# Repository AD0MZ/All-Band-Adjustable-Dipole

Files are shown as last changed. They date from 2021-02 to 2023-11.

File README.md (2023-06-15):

# All-Band-Adjustable-Dipole
### Motorized 10-80 Meter Adjustable Dipole 

-  A Self-Contained – Motorized Dipole Antenna System
-  Uses a Web-Based APP to set Element Lengths.  
-  Robust support for CAT and other Automation
-  Open Source – Using Open Source Tools

# Finished Product and APP!
- Antenna Winch on Tripod Mount.
  - Can Hang From a Rope or Use the Pole Mount Accesory.
- Node-Red Dashboard APP.  On Pixel 3 (Medium sized phone).

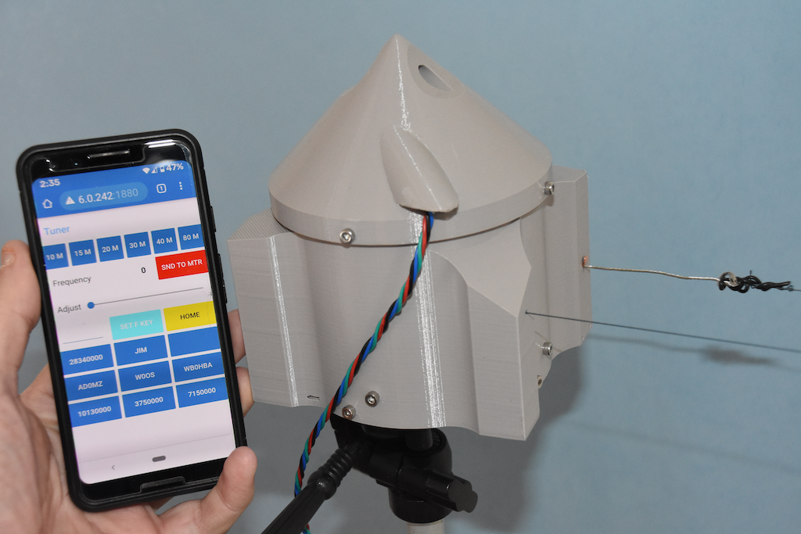
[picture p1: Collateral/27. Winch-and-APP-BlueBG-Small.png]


##### Inspiration
  - Interested in Antenna Physics since High School.
    - Particularly the concepts of Gain and Directivity when considering conservation of energy.
  - Recently interested in how Resonance and SWR affect Efficient Radiation.
  - Was surprised at how much better a friend’s antenna performed after a slight pruning.
    - We both noted how much better his dipole worked compared to his G5RV or his HexBeam Spiderweb.
  - Began thinking of an “automatic” self-pruning-dipole.
  - Hangar Door Openers!  
    - Realized that a creatively constructed “Capstan” combined with a clothesline-like element geometry would simplify the mechanics.
    - Airplane hangar door openers use a wire and drum geometry, and are the mechanical inspiration for the prototypes.
  - Needed a good Winter Project during “Covid - Stay at home”.

##### Learning from Those That Have Gone Before.
  - Article by AE4YW – Radiation is more important than SWR.
  - The RTV 80 by W4QJP and KC4TAQ  is a proven example of a complete adjustable system (But manually operated with adjustable ropes).
  - VA2ERY used a literal incarnation of a clothesline to move the feed-point of a folded dipole.
    - (Simple, but requires a balanced feed-line and a tuner.)
  - Collins Aerospace dual-drum winch for wire dipoles (Model 637-T1).
  - SteppIr.  Very successful stepper motor controlled Yagi’s, etc.
    - An automated – multi-element “Tape Measure” system if you look inside.

#### Status:  Two protoypes constructed and tested.  
  - Ready for constructive input and suggestions for improvement.  (More weatherproof?  Better / Simpler Stepper Control?  Etc?)

**Disclaimer:  I am a beginner with the tools I chose for this project, so it's as much a learning process as a production process.
  - I spent a lot of time quantifying and tuning my printer to make accurate parts.  The SCAD and STL files in this repository reflect
    pretty tight tolerances.  (The parts from my Prusa Mk3S had a nice friction fit and assembled without modification.)
    - (Parts printed on my friends Ender Pro were too big and required sanding and filing.)
    - If you use the STL's, print the first three layers of a few of the parts to see if things fit.

#### Tools Used:
  - OpenSCAD.  Wanted to learn it.  Experienced TurboCad Deluxe user, but it lacks proper 3D tools.
    - Tried FreeCad, but found it cumbersome.  (Tried others, but like the program-like build process.  Minutes to first useful object.
  - TurboCad.  Useful for initial 2D design to get precise measurements.
  - Wifi-Stepper Controller:  As a beginner with stepper control, Advanced feactures like acceleration and crash detection were beyond me.
    - The Wifi Stepper removes the complexity of comprehensive control and also provides simple interaces.  HTML, Bash, and Mqtt.

# Initial Concept:

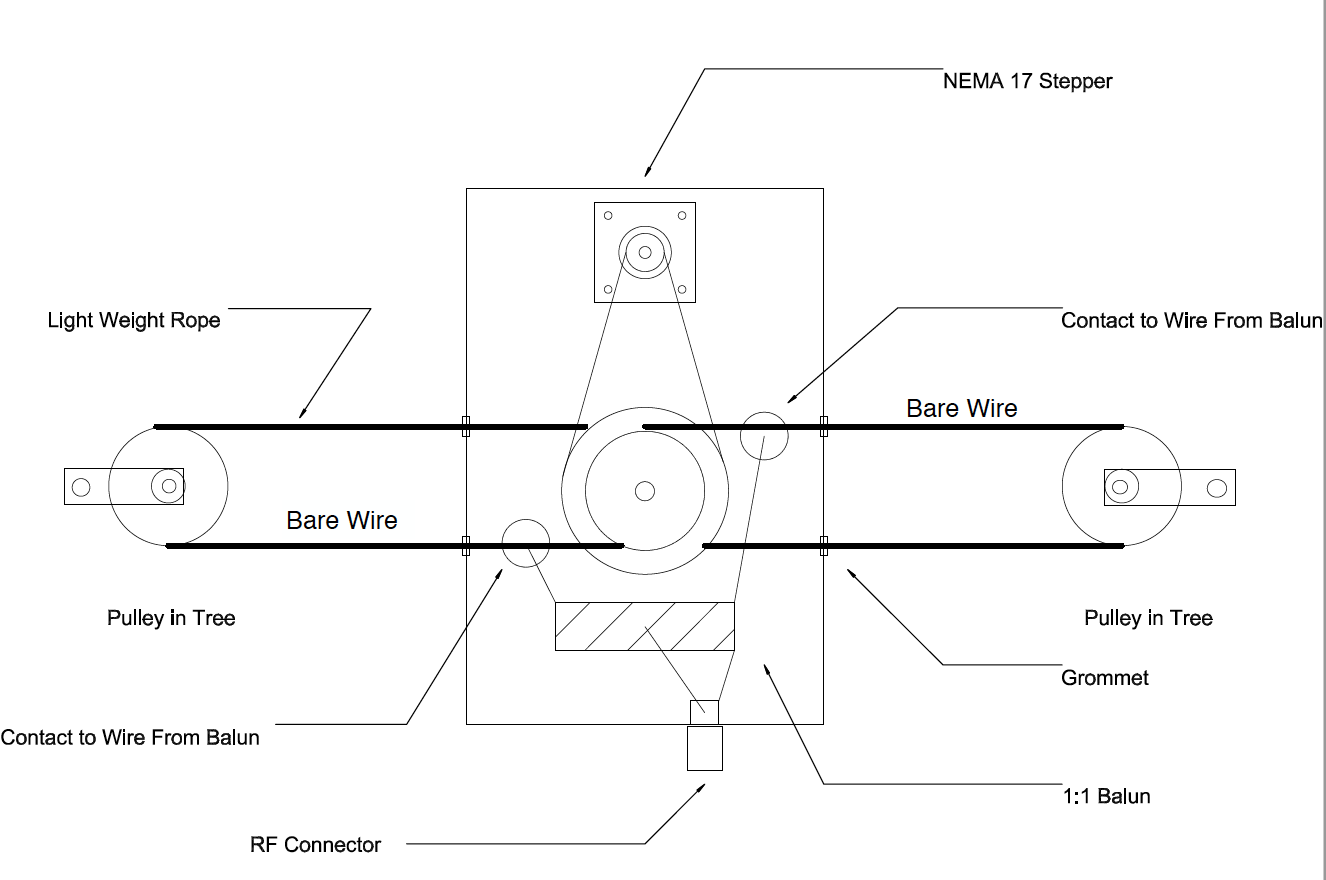
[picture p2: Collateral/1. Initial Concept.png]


# Animation of Kinematics
### Note that the wire (end at red dot) is wound out as a thin rope (Braided 60lb Fishing Line) is wound in (and in reverse).

All Band Adjustable Dipole

# Animation of a Sample Application.  (Node-Red Dashboard)

- The Flow lets the user select a band, then fine adjust it.  
  - A simple function calculates steps via simple math, and sends an absolute position to the motor. 
  
All Band Adjustable Dipole

# Bom:
  - (1) 8x22x7 MM sealed skateboard bearing
  - Assorted M3 screws and 16 thin square M3 nuts.
    - (14) M3-10 Button Head Screws (or cap-screws).
    - (4) M3-35 Button Head Screws (or cap-screws).
    - (16) M3 562 (S2) Thin - Flat Square nuts.
    - (2) M3 hex nuts.
  - (2) Generic (Makita CB-303 in my case) power tool brushes.
  - ~ 130 feet of 18 gauge tinned (less oxidation) wire.
  - ~ 260 feet of Nylon or Dacron 60lb test fishing line.
  - (4) pulleys (you can print them too), and some lightweight rope.
  - (2) 4mm x 1mm x 31mm copper strips.  (Wire guide slide surfaces.)
  - Glue compatible with plastic type.  (Top fasten top spool to middle spool.  Alignment pegs are on parts.)
    - Could add bosses and holes for screws on this part - was nervous about clearance for first unit. 
    - Bosses and holes on the improvement list.  (The part broke before the glue let go in my testing.)
  
  - Time to print:  ~40 hours.

  # Cutaway view of Internal Capstan Parts.
  
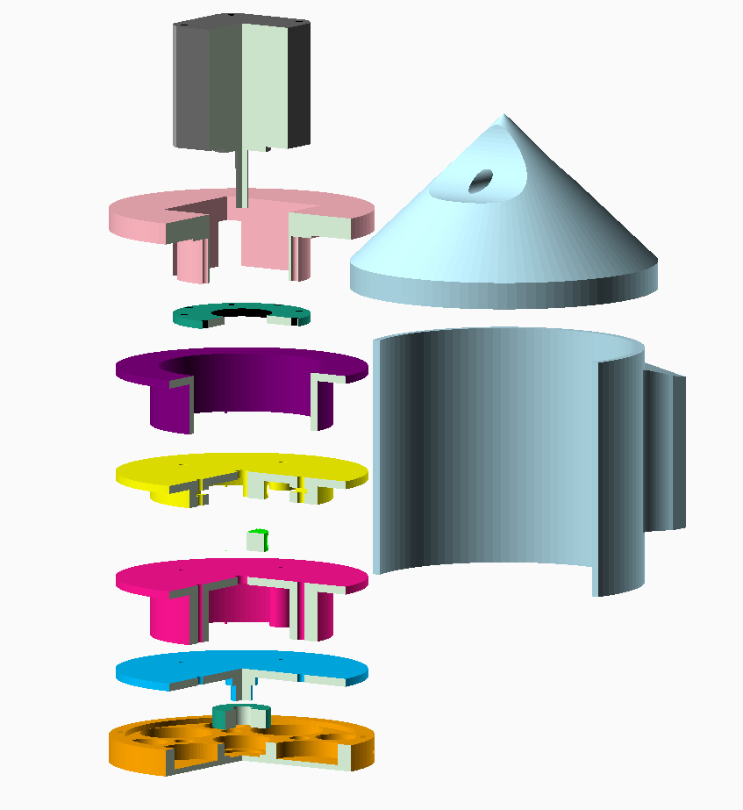
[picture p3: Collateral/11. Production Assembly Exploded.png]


# First Printed Parts
### Note:  First 3DP project! Trying different things.

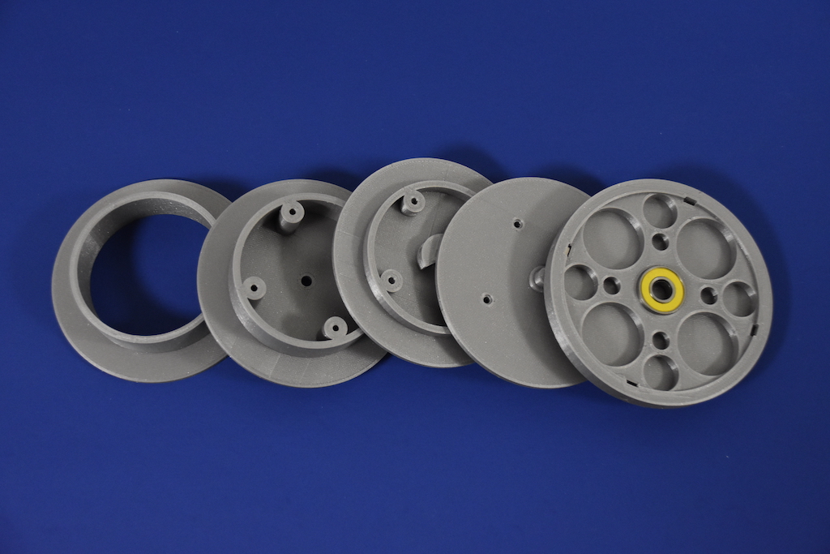
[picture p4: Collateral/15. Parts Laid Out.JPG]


# Brush Cartridge
- External for easy replacement.
  - Wires from balun or coax connect to cartridge only.  (Hole in bottom)
  - Optional base can house a balun or other gear, wire feeds through bottom of both parts to prevent water ingress.

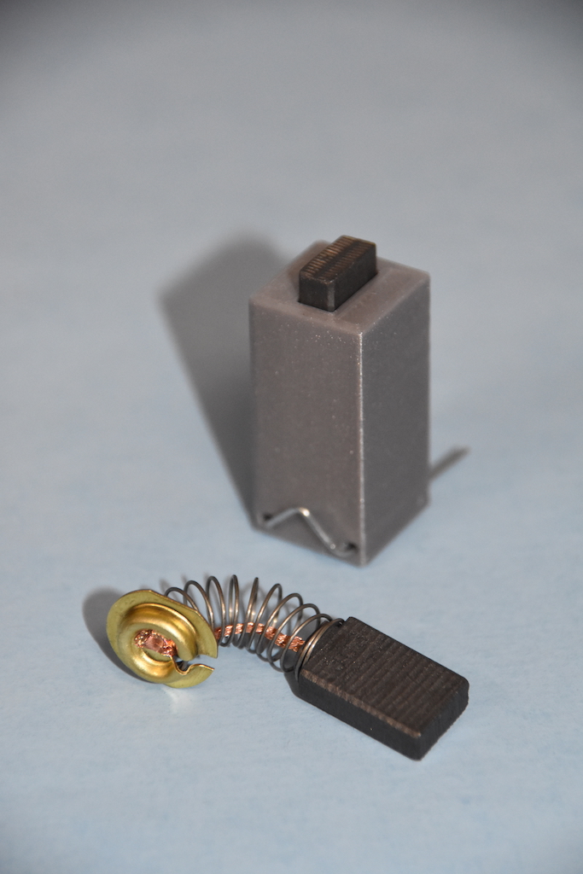
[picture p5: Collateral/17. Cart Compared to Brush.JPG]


# Brush Cartridges in place (almost) with Pole Mount and Balun Housing in place.  
- Housing pushed in to show brush carts better!

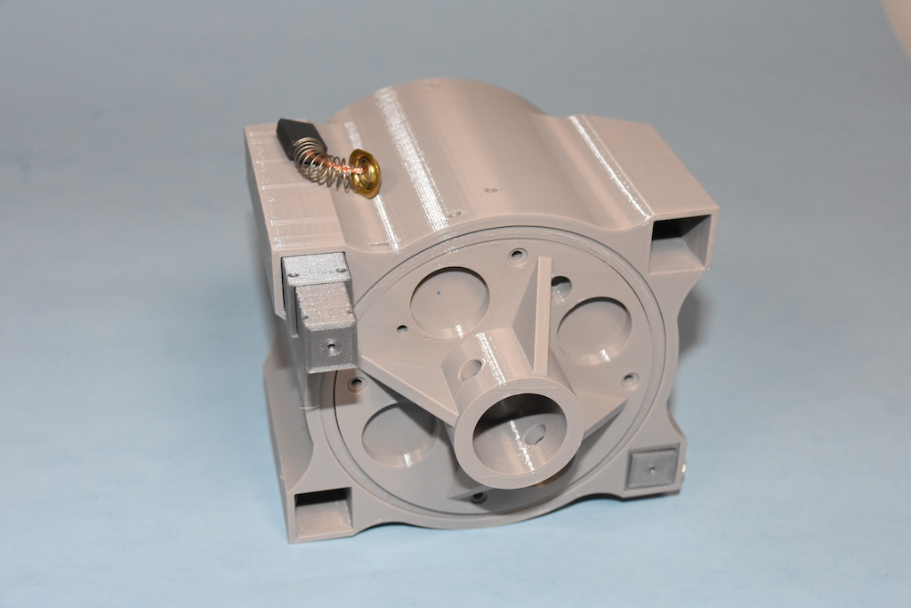
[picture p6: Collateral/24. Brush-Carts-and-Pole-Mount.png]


# VNA (un-calibrated :-)  ) scanning 13Mhz to 15Mhz when antenna is tuned to 14.220 Mhz

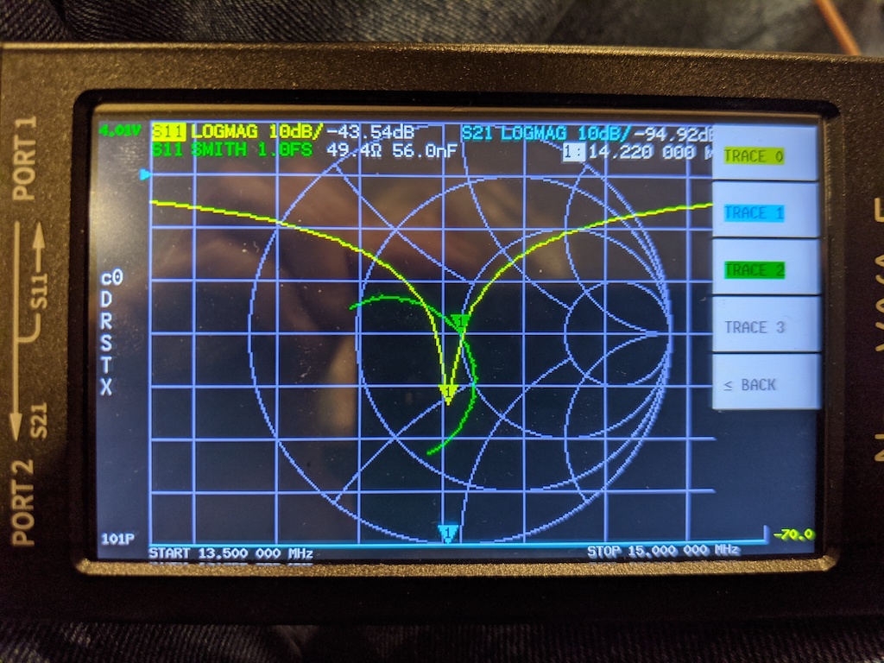
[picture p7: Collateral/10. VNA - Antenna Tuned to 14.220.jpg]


# Similar Antennas / Prior Work
- Collins 637t-1.
- Center Adjustable Folded Clothesline Dipole.
- RTV 80 Inverted V.

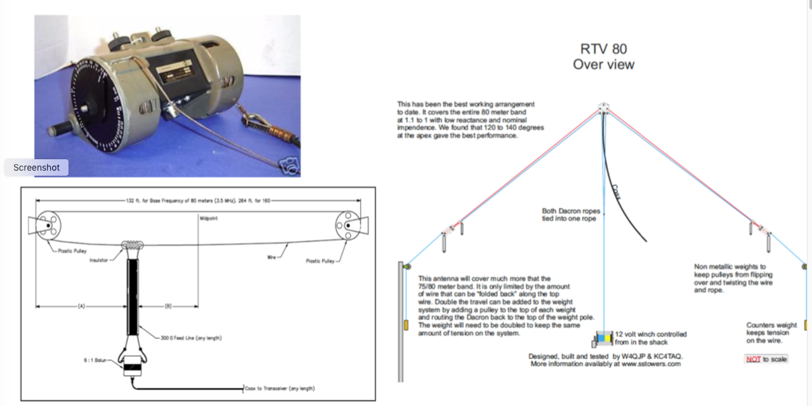
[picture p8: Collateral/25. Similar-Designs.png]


# Winch / Controller Closeup.

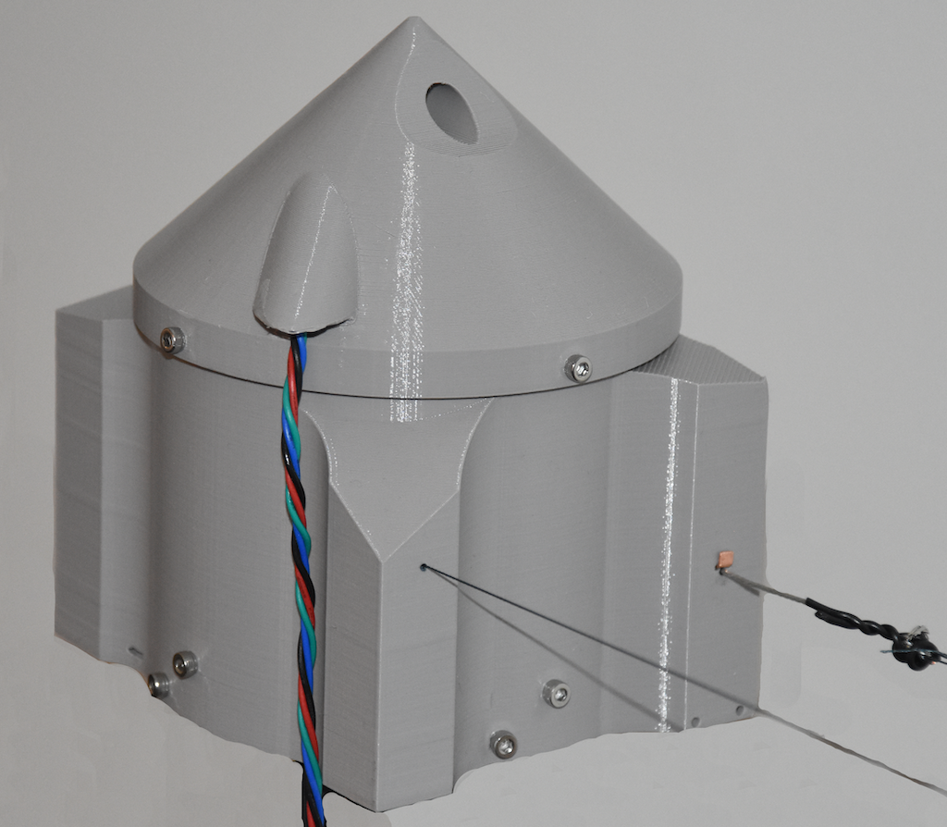
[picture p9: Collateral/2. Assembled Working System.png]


# Arrangement of commutators (brushes) with elements (wires).
- A few people have asked me why the brushes are on the "outside" of the capstan mechanism.
- One friend asked about the use of bare wire rather than insulated.
    - It turns out that the location of the brushes and the issues of insulated (or un-insulated) wire are related.

Early on, I had envisioned internal brushes on a commutating ring like an automotive alternator, 
with the use of insulated wire elements.
- I soon realized that the coiled-up element wires would make an excellent inductor at the frequencies we operate at.
- I was uncertain of how the brushes would wear, and how certain meterials might conduct at RF. 
    - I wanted to have an easy way to change them and experiment.
- Using un-insulated wire and external brushes solved every fatal problem and only introduced a couple of minor ones.
    _ (1.  Corrosion    2.  Loss of signal to things that touch the wire like leaves? )
    
Here are two diagrams I used to demonstrate the issues to a very smart friend.

Final design:
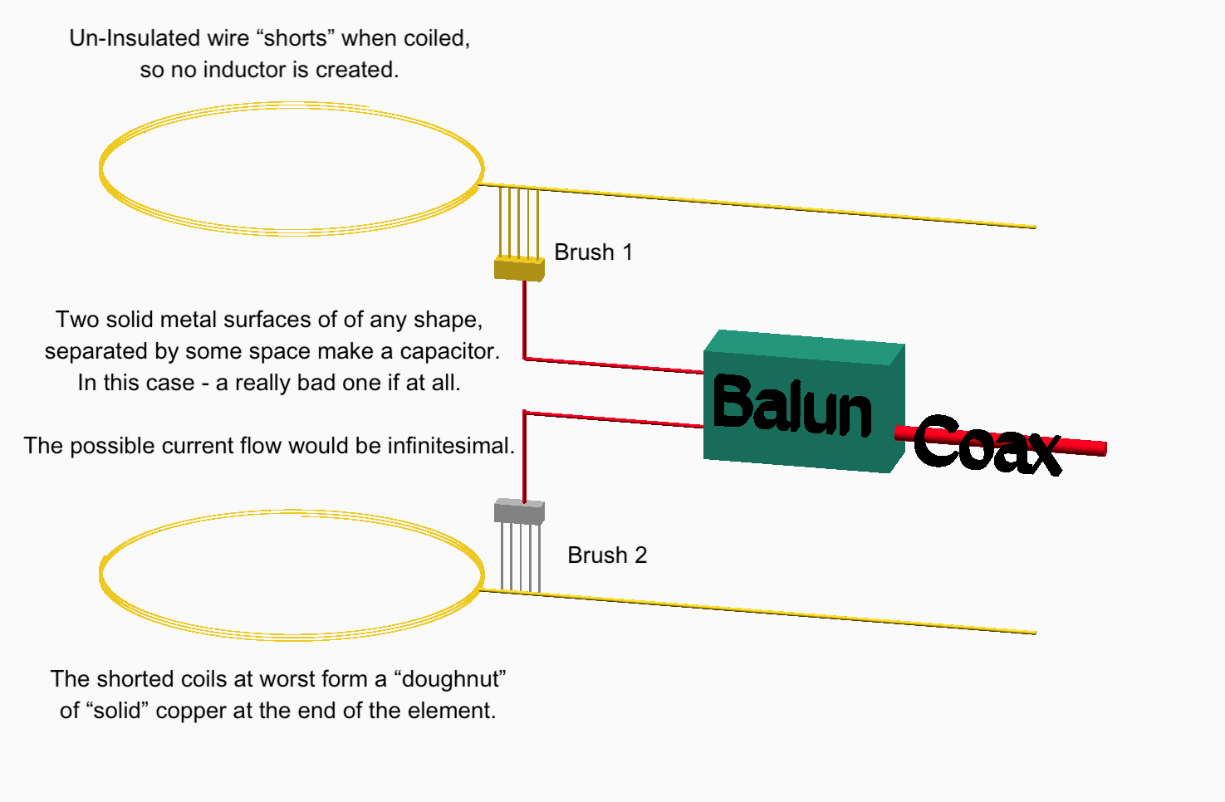
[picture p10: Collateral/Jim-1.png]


Contemplated design:
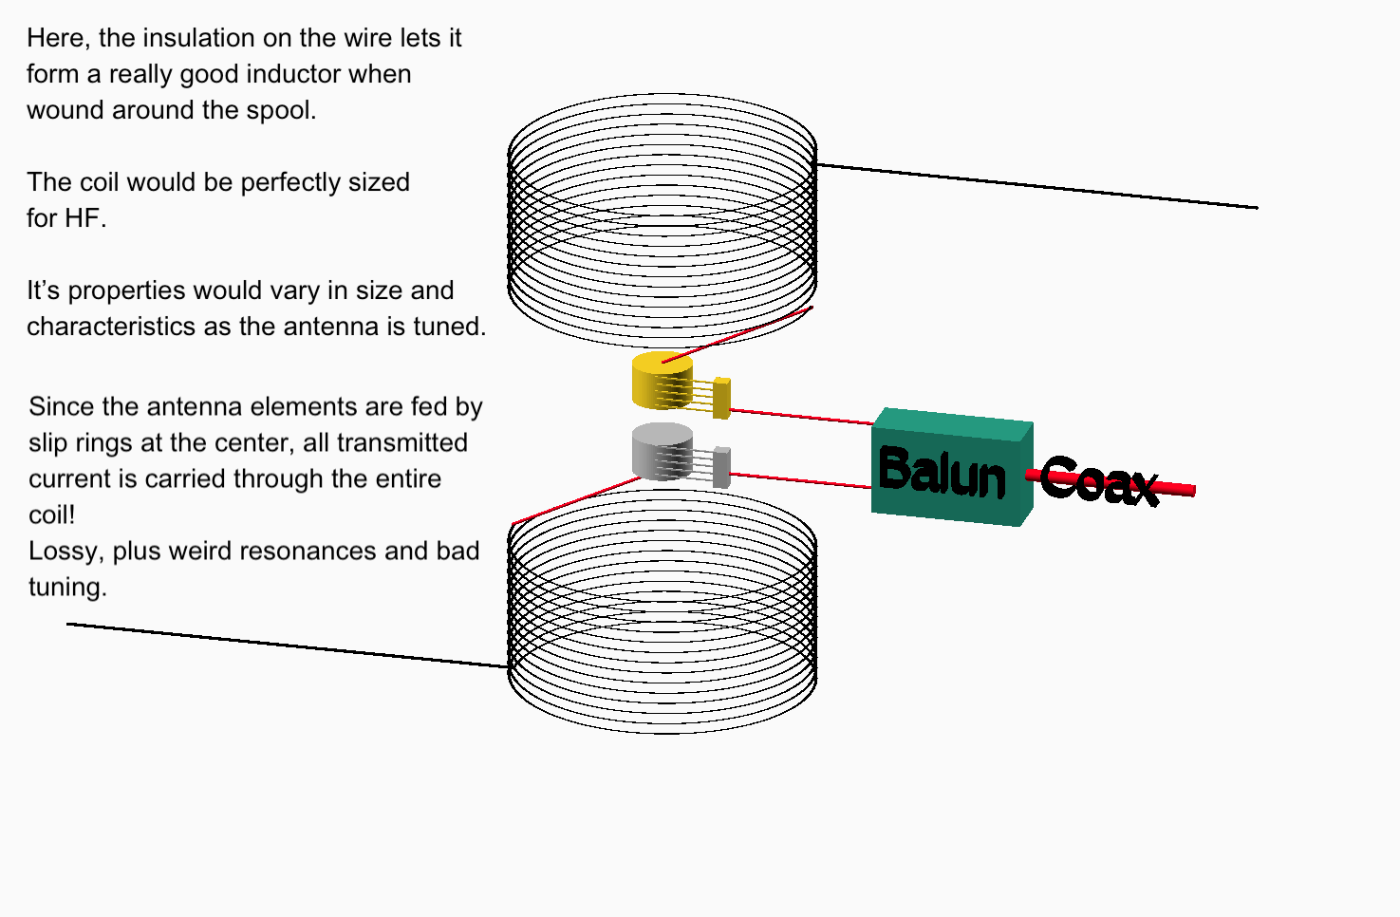
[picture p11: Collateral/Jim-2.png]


# It would be fun to model the "insulated wire - central commutator" design to see if it would be tunable across all bands with wierd  but shorter element lengths.
- Software could then pick the memorized lengths for each band with micro-tuning control still available.
- The coiled wire on spools could act as loading coils, with more coil at shorter element lengths.

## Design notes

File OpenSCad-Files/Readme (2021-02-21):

# The various plastic parts.

## This is my first OpenSCAD project, so I learned as I went.

### Planned work.

1.  Improve and spell check to comments, adding better documentation of pourpose and better explaination of spaghetti code.
2.  Start cleaning up variouis modules to better paraterize them, including more constants with variables in constructs.
    - First functional improvment - add some holes in the flanges of the spools to make ataching the wires and ropes without disassembly is possible and easy.

#### The topmost capstan parts were the first to be modeled, working towards the bearing plate, and the back up to the motor mount.
     - I hope to redo them all to be more "paramterized" and more modular.  (Lots of spaghetti code on some...)  
     - Will go though them as time permits and improve the comments as well.
  
- My workflow...  (Some not implemented yet  :-)   )
  - Draw the proposed system in 2D using TurboCad to get good measurements and to help visualize.
    - Tried FreeCad, TinkerCad, and others - the learining curve was too steep after 20 years of TurboCad.
      -  After two days with FreeCad and giving up,  Had a set of capstan spools completed with OpenSCAD in a few hours!
  - Design the solid parts and combine into a module.
  - Design the shapes that will be subtracted for holes and such and place into a module or two.
  - Combine the two into another module with "difference ()"
  - Call out the main module so it shows.
  - Try to use unique names (not competed) so that "include" can be used to assemble parts into views easier.

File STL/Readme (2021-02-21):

The main case file gives a manifold error in OpenSCAD, util a very minor hole is eliminated.  (Screw_holes).
Other tools proclaim it OK, and it prints fine.  On the list to debug further, but since I dropped the entire tuner onto concrete from high up and cracked it - I wanted to reprint instead of debug.

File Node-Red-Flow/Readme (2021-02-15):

The Main Flow for the Tuner, and a test set of utilities to set controller parameters.

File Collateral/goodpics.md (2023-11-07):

<table>
<tr>
<th>1970's Sansui 55 Watt Audiopile Amp  </td>
<th>Print of Famous Guardian Angel Painting</td>
<th>15 Speed Bike</br>Was called a "Girls Bike" back in the days.</td>
</tr>

<tr>
<td valign="top">
<a href="./GoodPics/Amp.jpg">
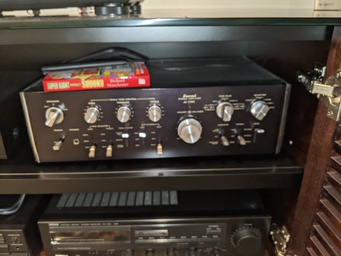
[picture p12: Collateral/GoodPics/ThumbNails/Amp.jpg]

</a>
</td>

<td valign="top">
<a href="./GoodPics/Angel-Guide.jpg">
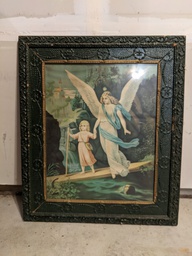
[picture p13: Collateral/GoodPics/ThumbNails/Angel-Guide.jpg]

</a>
</td>

<td valign="top">
<a href="./GoodPics/BIke.jpg">
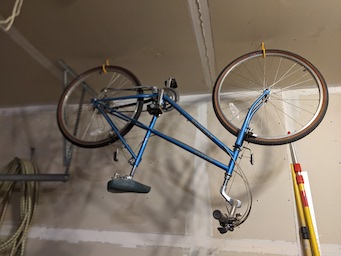
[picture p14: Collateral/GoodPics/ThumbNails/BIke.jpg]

</a>
</td>
</table>

<table>
<tr>
<th>Full-Featured Bernina Sewing Machine (Value Model) </td>
<th>Classic 8mm Bolex Movie Camera</td>
<th>Same Bolex showing four lenses</td>
</tr>

<tr>
<td valign="top">
<a href="./GoodPics/Bernina.jpg">
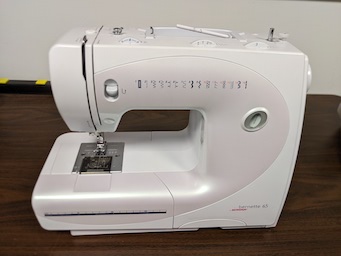
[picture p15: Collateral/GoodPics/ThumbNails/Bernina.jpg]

</a>
</td>

<td valign="top">
<a href="./GoodPics/Bolex-1.jpg">
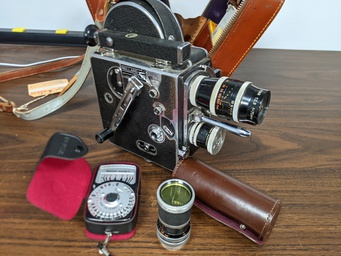
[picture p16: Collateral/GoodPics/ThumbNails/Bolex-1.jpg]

</a>
</td>

<td valign="top">
<a href="./GoodPics/Bolex-2.jpg">
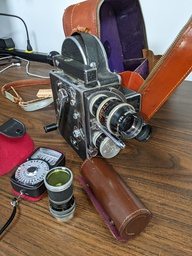
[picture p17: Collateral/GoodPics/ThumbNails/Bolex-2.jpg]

</a>
</td>

</table>

<table>
<tr>
<th>Original Box for Bolex</td>
<th>Yamaha Cassette Player (Part of Component Set)</td>
<th>Antique Corn Planter (Really old)</td>
</tr>
  
<tr>
<td valign="top">
<a href="./GoodPics/Bolex-3.jpg">
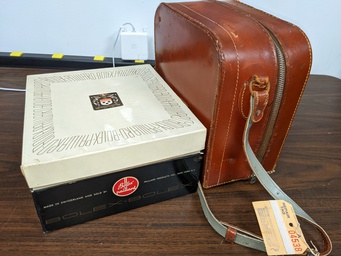
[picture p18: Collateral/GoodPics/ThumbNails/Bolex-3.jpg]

</a>
</td>

<td valign="top">
<a href="./GoodPics/Cassette.jpg">
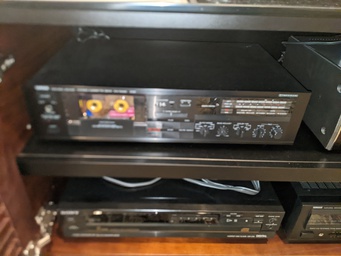
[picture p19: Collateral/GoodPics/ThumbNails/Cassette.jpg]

</a>
</td>

<td valign="top">
<a href="./GoodPics/Corn-Planter.jpg">
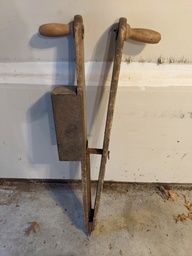
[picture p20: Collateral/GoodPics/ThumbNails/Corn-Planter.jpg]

</a>
</td>
</tr>

</table>

<table>
<tr>
<th>Portrait of Euphamia Strandjord (I Think)</td>
</tr>
  <tr>
<td valign="top">
<a href="./GoodPics/Euphamia.jpg">
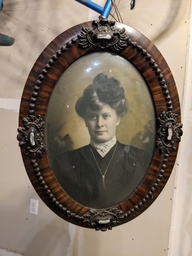
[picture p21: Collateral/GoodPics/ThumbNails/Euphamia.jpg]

</a>
</td>
</tr>
</table>

<table>

<tr>
<th>Mac Pro - Core Duo</br> New battery</br>Clean HD + MSOFFICE</br>Good for email and web)</td>
<th>Yamaha Receiver (part of set)</td>
<th>Shop Vac</td>
</tr>

<tr>
<td valign="top">
<a href="./GoodPics/Mac-Pro.jpg">
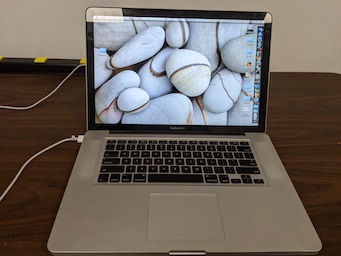
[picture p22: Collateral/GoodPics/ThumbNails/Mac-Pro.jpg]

</a>
</td>

<td valign="top">
<a href="./GoodPics/Receiver.jpg">
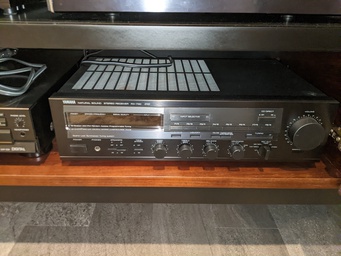
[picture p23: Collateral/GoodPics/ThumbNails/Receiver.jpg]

</a>
</td>

<td valign="top">
<a href="./GoodPics/Shop-Vac.jpg">
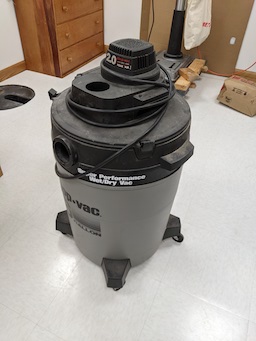
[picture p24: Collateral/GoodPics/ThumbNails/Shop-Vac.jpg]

</a>
</td>

</table>

<table>
<tr>

<th>Singer Featherweight (Restored)</td>
  <th>Sony 5 disk CD Player</th>
</tr>

<tr>

<td valign="top">
<a href="./GoodPics/Singer.jpg">
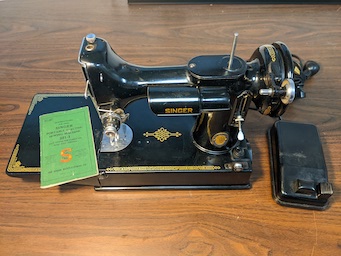
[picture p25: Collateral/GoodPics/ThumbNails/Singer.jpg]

</a>
</td>

<td valign="top">
<a href="./GoodPics/Sony-CD.jpg">
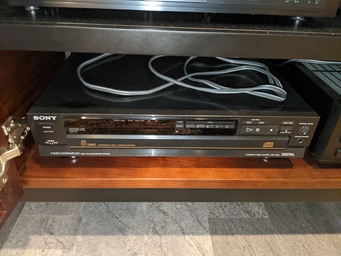
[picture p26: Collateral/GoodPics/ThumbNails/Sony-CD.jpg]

</a>
</td>
</tr>

</table>

<table>
<tr>
<th>Speakers - Klipsh Forte  </br>Mellow -- Classical Music, on left)</br></br> Keeping the Classic Pioneer HPM 100's </br>Google Them!</br>(Crisp -- Rock, etc. on  right)</td>
<th>Lenovo T510 Busines Class Laptop</br> (As new - Clean)</td>
<th>Table Saw (Recently refurbished)</td>
</table>tr>
<tr>
<td valign="top">
<a href="./GoodPics/Speakers.jpg">
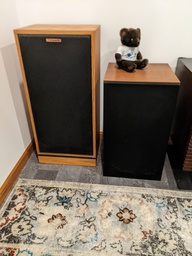
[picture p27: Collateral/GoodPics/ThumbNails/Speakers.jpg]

</a>
</td>

<td valign="top">
<a href="./GoodPics/T510.jpg">
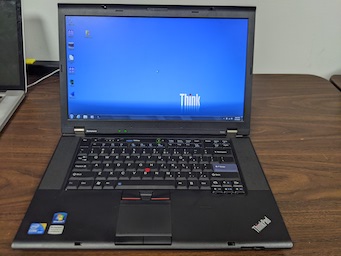
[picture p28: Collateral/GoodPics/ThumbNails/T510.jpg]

</a>
</td>

<td valign="top">
<a href="./GoodPics/Table-Saw.jpg">
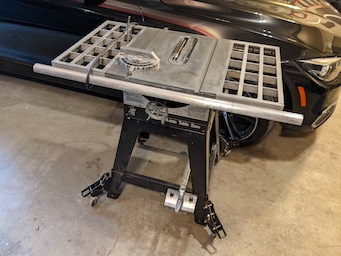
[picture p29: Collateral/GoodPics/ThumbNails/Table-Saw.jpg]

</a>
</td>
</tr>
</table>

<table>
<tr>
<th>Celeston Refracting Telescope</td>
<th>Restored Marx HO Train</br>Rare Classic with Extra Track, etc.)</td>
</tr>
<tr>  
<td valign="top">
<a href="./GoodPics/Telescope-1.jpg">
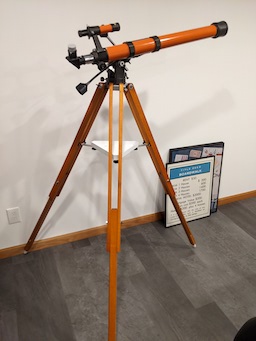
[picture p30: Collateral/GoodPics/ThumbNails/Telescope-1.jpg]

</a>
</td>

</table>

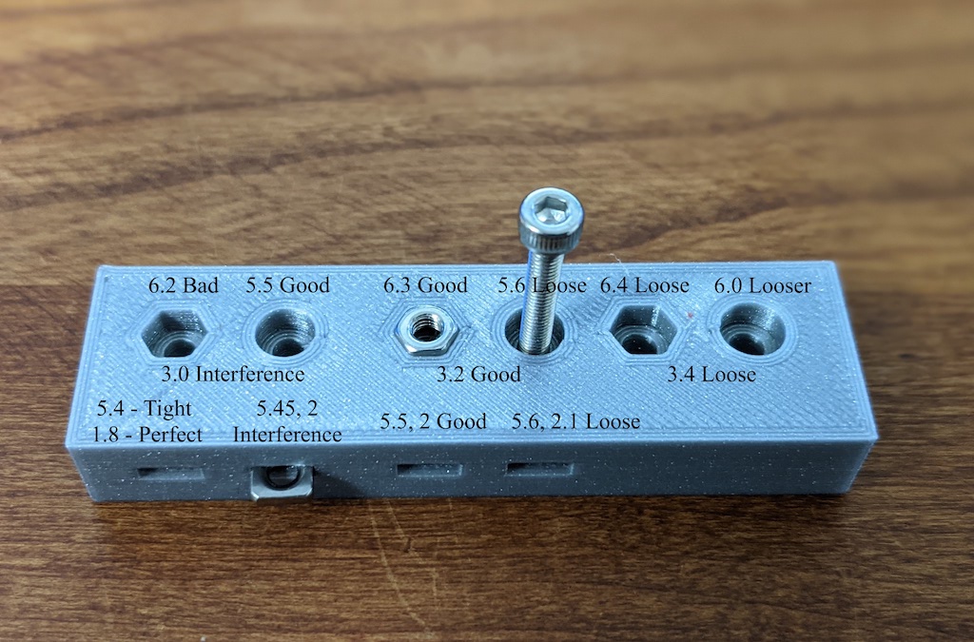
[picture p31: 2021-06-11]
Pictures/Not-and-Bolt-Holes.jpg

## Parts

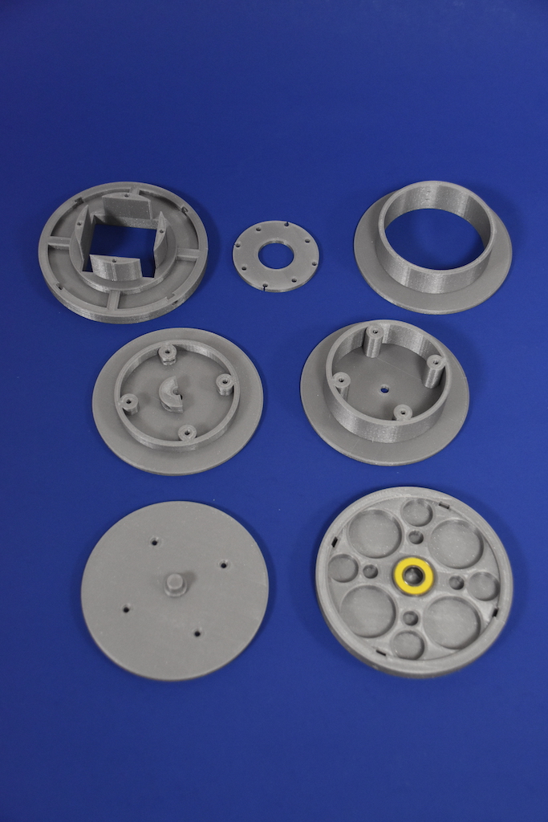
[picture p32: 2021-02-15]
Collateral/14. Printed Production Parts 1.JPG

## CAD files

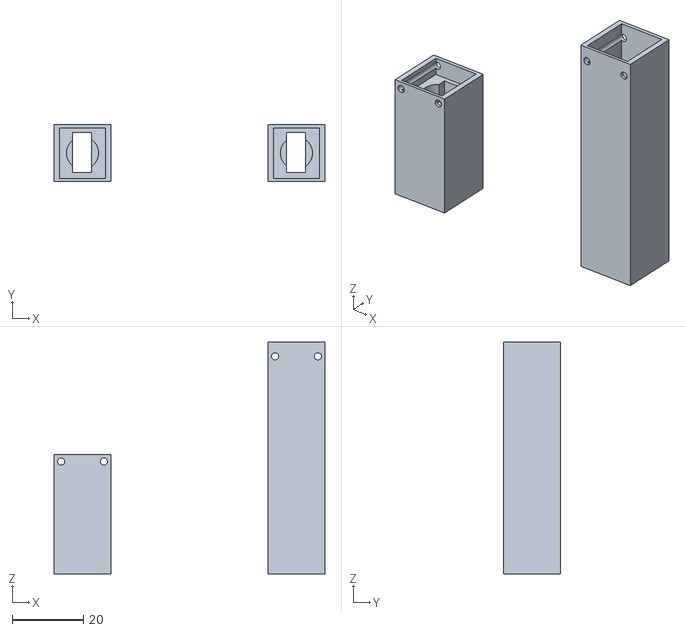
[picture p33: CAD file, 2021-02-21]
STL/Brush-Cart-Assembly-V1.0.stl
76.0 x 16.0 x 65.0

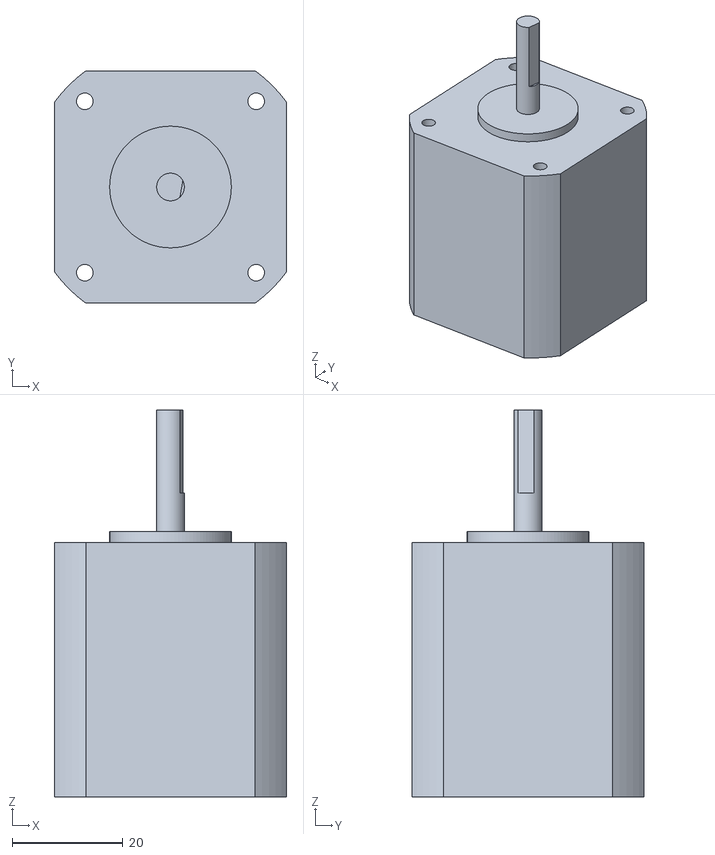
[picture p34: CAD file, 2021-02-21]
STL/Nema-17-Motor-V1.0.stl
42.0 x 42.0 x 70.0

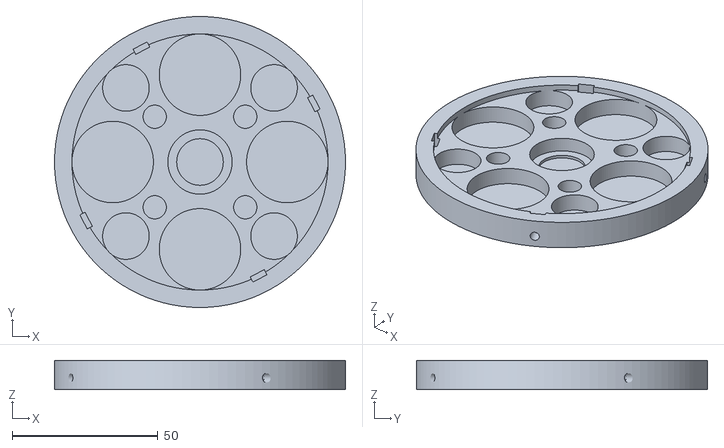
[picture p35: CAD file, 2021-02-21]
STL/Base-Plate-V1.0.stl
100.0 x 100.0 x 10.0

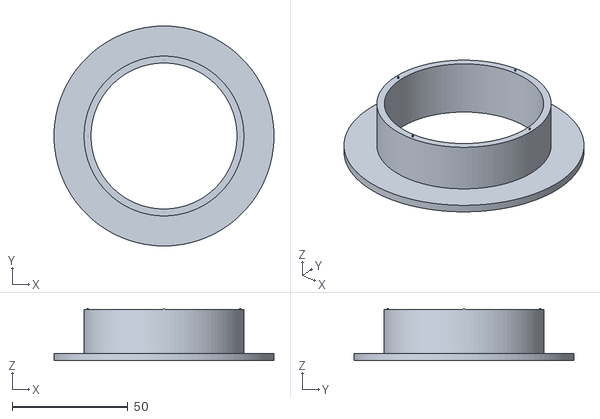
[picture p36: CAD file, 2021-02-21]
STL/Top-Flange-V1.0.stl
95.0 x 95.0 x 22.5

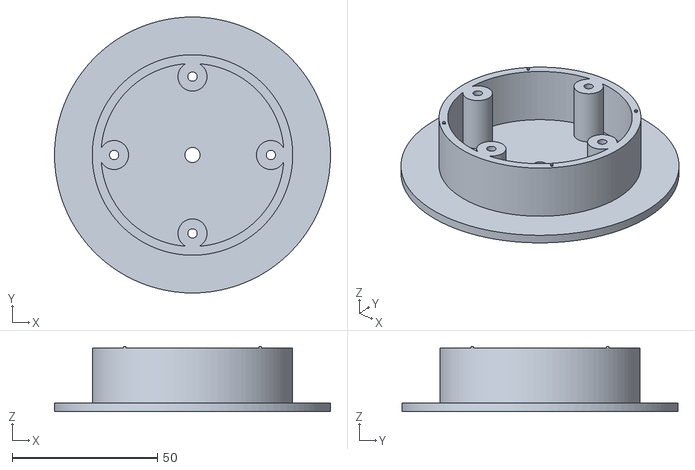
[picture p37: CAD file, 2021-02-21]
STL/Bottom-Flange-V1.0.stl
95.0 x 95.0 x 22.5

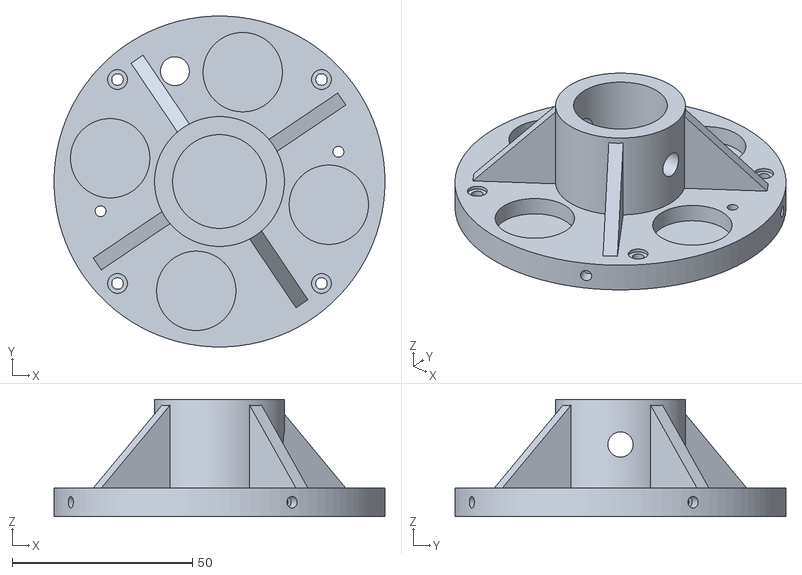
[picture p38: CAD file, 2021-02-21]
STL/Base-Mount-4-Pipe-V1.0.stl
91.8 x 91.8 x 32.5

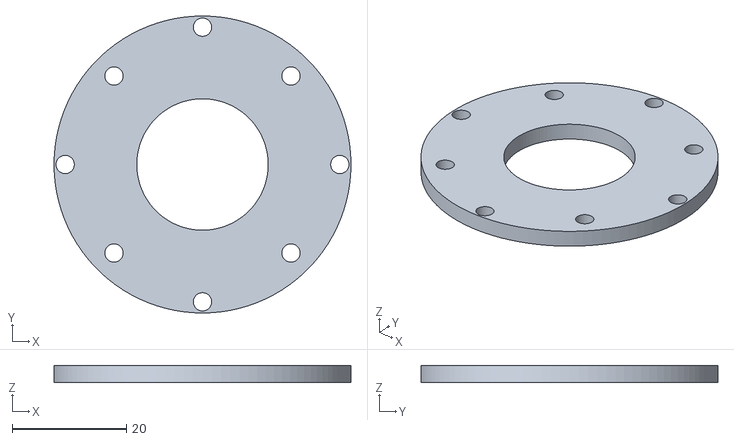
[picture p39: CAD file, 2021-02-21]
STL/Motor-Plate-V1.0.stl
52.0 x 52.0 x 3.00

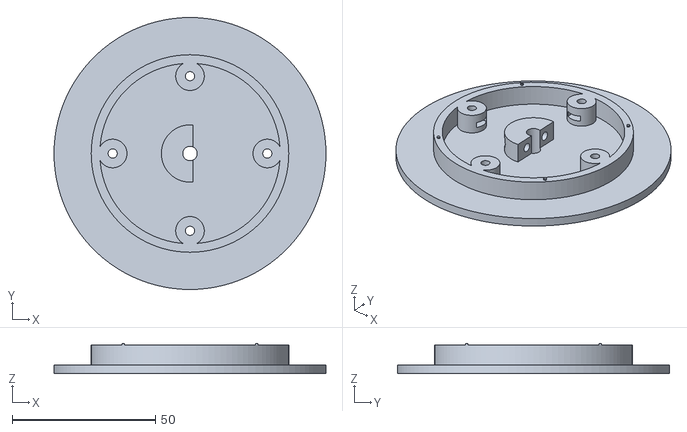
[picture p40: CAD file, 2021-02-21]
STL/Middle-Flange-V1.0.stl
95.0 x 95.0 x 10.5

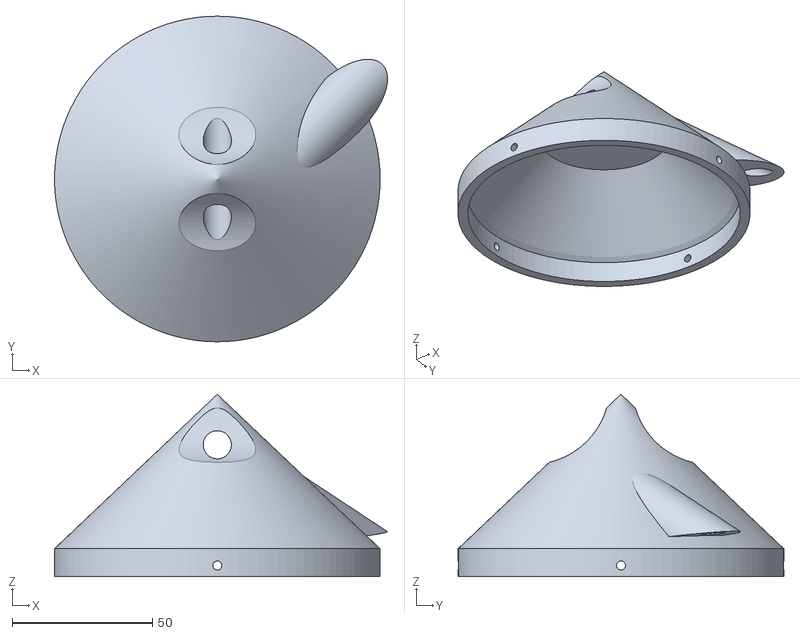
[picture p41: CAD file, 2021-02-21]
STL/Top-Cone-V1.0.stl
118.6 x 116.0 x 65.0

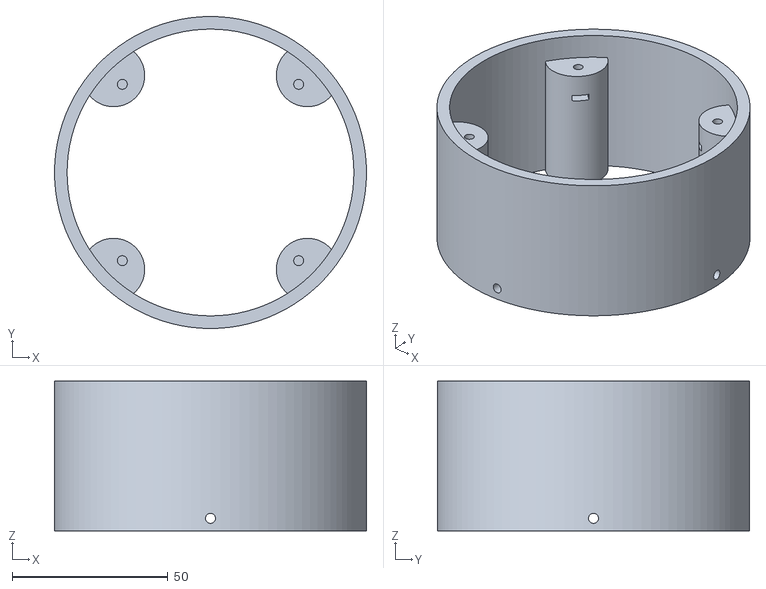
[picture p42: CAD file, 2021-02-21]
STL/Base-Mount-Ring-V1.0.stl
100.1 x 100.1 x 48.0

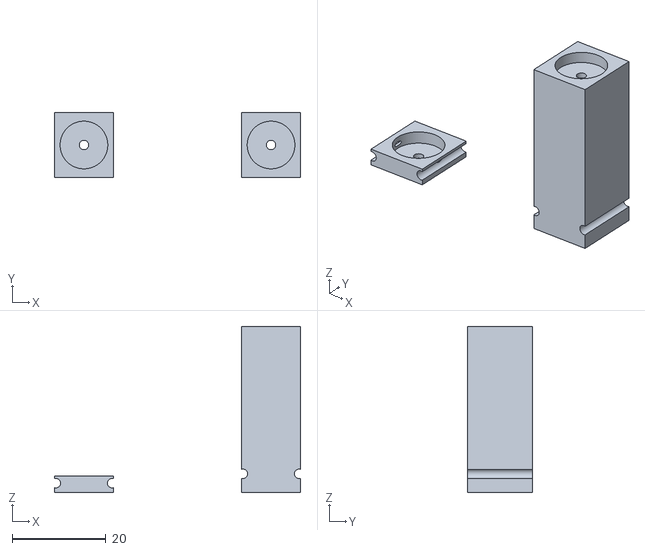
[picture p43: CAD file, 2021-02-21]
STL/Plugs-V1.0.stl
52.6 x 13.8 x 35.5

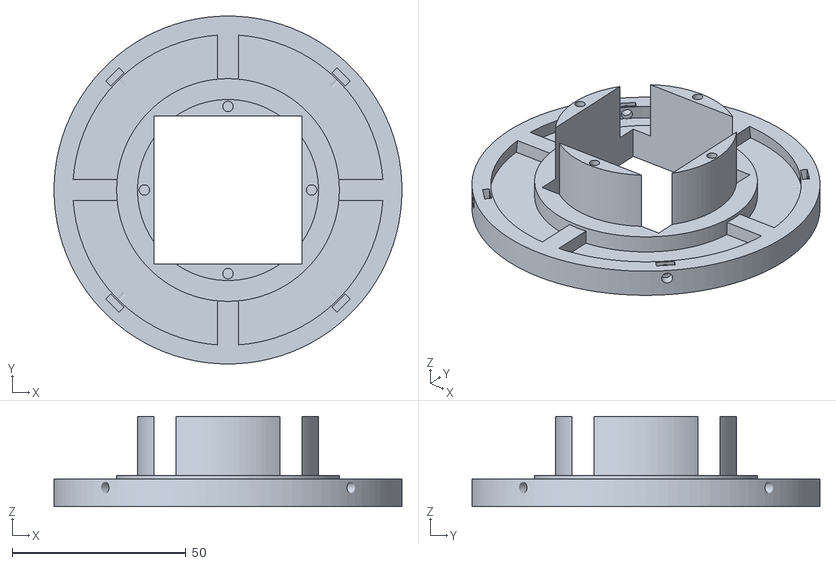
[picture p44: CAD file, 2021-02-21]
STL/Motor-Mount-Ring-V1.0.stl
100.0 x 100.0 x 26.0

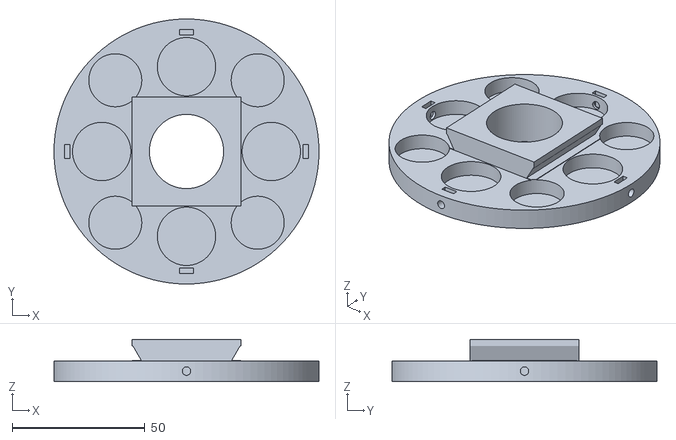
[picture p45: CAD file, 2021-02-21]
STL/Tripod-Mount-1.0.stl
100.0 x 100.0 x 16.0

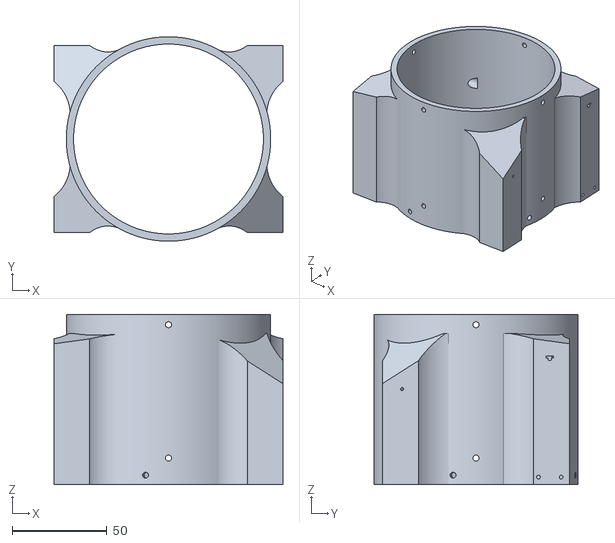
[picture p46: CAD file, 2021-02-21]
STL/Case-With-Brush-Carts-V1.0.stl
121.0 x 108.0 x 90.0

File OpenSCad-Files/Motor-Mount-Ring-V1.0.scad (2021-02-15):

$fa=1;
// V 2.1 adds square nut holes and makes the outer righ a bit thicker on the inside.  


include <nut and Bolt Holes.scad>

module boss_cylinder (){
	cylinder (26,26,26);
}
module webs () {
			translate ([-3,31,0])
				cube ([6,16,5]);
			translate ([-3,-47,0])
				cube ([6,16,5]);
			translate ([-47,-3,0])
				cube ([16,6,5]);
			translate ([31,-3,0])
				cube ([16,6,5]);
}
module plate_holes () {
color ("Black"){
			translate ([17,17,0])
				cylinder (26.02,1.5,1.5);
			translate ([17,-17,0])
				cylinder (26.02,1.5,1.5);
			translate ([-17,17,0])
				cylinder (26.02,1.5,1.5);
			translate ([-17,-17,0])
				cylinder (26.02,1.5,1.5);
			}
}

module motor_bosses (){
	difference (){
		boss_cylinder ();
		translate ([0,0,-.01])
		rotate (45,[0,0,1])
		plate_holes ();
		
	}
}




module ring_mount (){
difference (){
cylinder (8,50,50);
translate ([0,0,4])
cylinder (5,45,44.5);
}
}

module inner_ring (){
cylinder (5,32,32);
}

// Create a "virtual ring" of holes for the nuts and screws.  Added to the "Difference" module later.  Easest to rotate them into correct orientation, and then move them out a fixed amount from center (no math!).
module nut_ring_holes (){
		translate ([42,0,0])
			rotate (-90,[0,0,1])
			rotate (-90,[1,0,0])
			m3_square_nut_WFB ();

		translate ([-42,0,0])
		rotate (90,[0,0,1])
		rotate (-90,[1,0,0])
			m3_square_nut_WFB ();

		translate ([0,-42,0])
		rotate (180,[0,0,1])
		rotate (-90,[1,0,0])
			m3_square_nut_WFB ();

		translate ([0,42,0])
		rotate (0,[0,0,1])
		rotate (-90,[1,0,0])
			m3_square_nut_WFB ();
}


module adder (){
ring_mount ();
motor_bosses () ;	
translate ([0,0,4])
inner_ring ();

translate ([0,0,3])
webs();
}

module motor_mount_ring (){
difference (){
	adder ();
	cube ([42.5,42.5,85], center = true);
	translate ([0,0,5.5])
		rotate (45,[0,0,1])
		nut_ring_holes ();
}
}

motor_mount_ring ();

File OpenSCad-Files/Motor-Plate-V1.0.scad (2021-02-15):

$fn=100;

module main_plate (){
	cylinder (3,26,26);
}


// V 2.1 increased size of holes to 1.6 from 1.5
// V 202 incfreased the size of the center motor hole

module motor_holes () {
color ("Black"){
			translate ([15.5,15.5,0])
				cylinder (16.02,1.6,1.6);
			translate ([15.5,-15.5,0])
				cylinder (16.02,1.6,1.6);
			translate ([-15.5,15.5,0])
				cylinder (16.02,1.6,1.6);
			translate ([-15.5,-15.5,0])
				cylinder (16.02,1.6,1.6);

				cylinder (3.02,11.5,11.5);
			}
}
module plate_holes () {
color ("Black"){
			translate ([17,17,0])
				cylinder (16.02,1.6,1.6);
			translate ([17,-17,0])
				cylinder (16.02,1.6,1.6);
			translate ([-17,17,0])
				cylinder (16.02,1.6,1.6);
			translate ([-17,-17,0])
				cylinder (16.02,1.6,1.6);
			}
}

module motor_plate (){
difference (){
main_plate ();
translate ([0,0,-.01])
motor_holes ();
translate ([0,0,-.01])
rotate (45,[0,0,1])
plate_holes ();
}
}
motor_plate() ;

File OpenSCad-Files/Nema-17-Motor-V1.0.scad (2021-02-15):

$fn=100;
  


module chamfer (){
	// Used to build rounded edges of motor body
		translate ([0,0,-.01])
			difference () {
				cylinder (46.02,35,35);
				cylinder (46.02,26,26);
			}
}

module shaft (){
	// Cuts the flat part into the shaft
		difference (){
			cylinder (22,2.5,2.5);
			translate ([-2.5,2,7])
				cube ([5,5,22]);
		}
}

	

module motor (){
// Draws the main body - and chamfers and adds the holes and shaft.
		difference (){
			 translate ([-21,-21,0]) 
				color ("DarkGray")
					cube ([42,42,46]);
				color ("DarkGray")
			  chamfer ();

    //Screw Holes
		color ("Black"){
			translate ([15.5,15.5,-.01])
				cylinder (46.02,1.5,1.5);
			translate ([15.5,-15.5,-.010])
				cylinder (46.02,1.5,1.5);
			translate ([-15.5,15.5,-.01])
				cylinder (46.02,1.5,1.5);
			translate ([-15.5,-15.5,-.01])
				cylinder (46.02,1.5,1.5);
			}
}
	
	// Bearing Boss
		translate ([0,0,46])
			color ("LightGray")
			cylinder (2,11,11);
	// Position Shaft on Top
		translate ([0,0,48])
		rotate (-100,[0,0,1])
			color ("Gainsboro")
			shaft ();
}
// END MOTOR

//  Draw the whole thing.
motor ();

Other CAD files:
STL/Hub-Lock-V1.0.stl
STL/Bearing-Flange-V1.0.stl
OpenSCad-Files/Base-Mount-4-Pipe-V1.0.scad
OpenSCad-Files/Base-Mount-Ring-V1.0.scad
OpenSCad-Files/Base-Plate-V1.0.scad
OpenSCad-Files/Bearing-Flange-V1.0.scad
OpenSCad-Files/Bottom-Flange-V1.0.scad
OpenSCad-Files/Brush-Cart-Assembly-V1.0.scad
OpenSCad-Files/Case-With-Brush-Carts-V1.0.scad
OpenSCad-Files/Hub-Lock-V1.0.scad
OpenSCad-Files/Middle-Flange-V1.0.scad
OpenSCad-Files/Nut and Bolt Holes.scad
OpenSCad-Files/Plugs-V1.0.scad
OpenSCad-Files/Top-Cone-V1.0.scad
OpenSCad-Files/Top-Flange-V1.0.scad
OpenSCad-Files/Tripod-Mount-1.0.scad

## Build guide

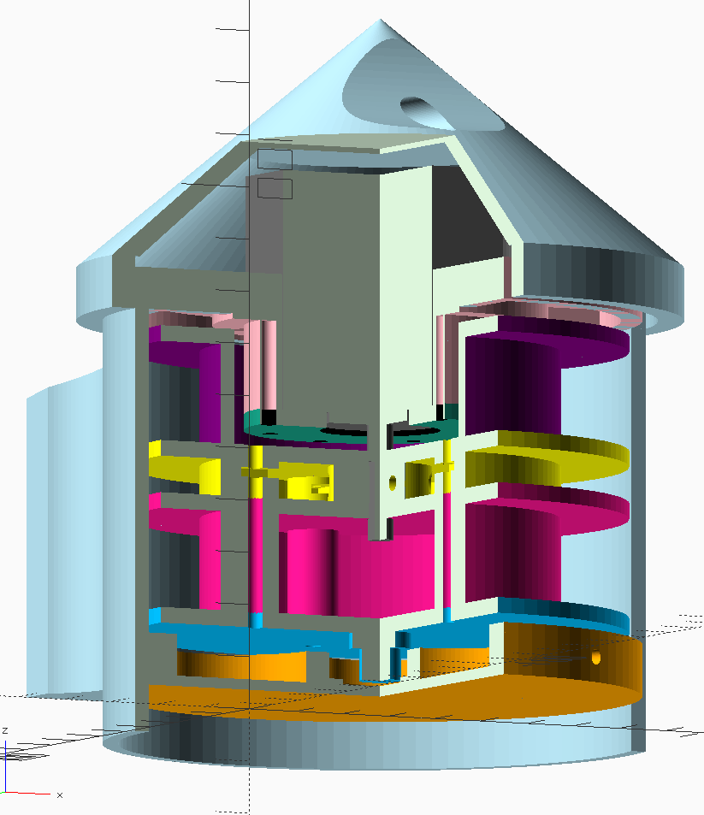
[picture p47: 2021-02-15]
Collateral/12. Assembly Cutaway.png

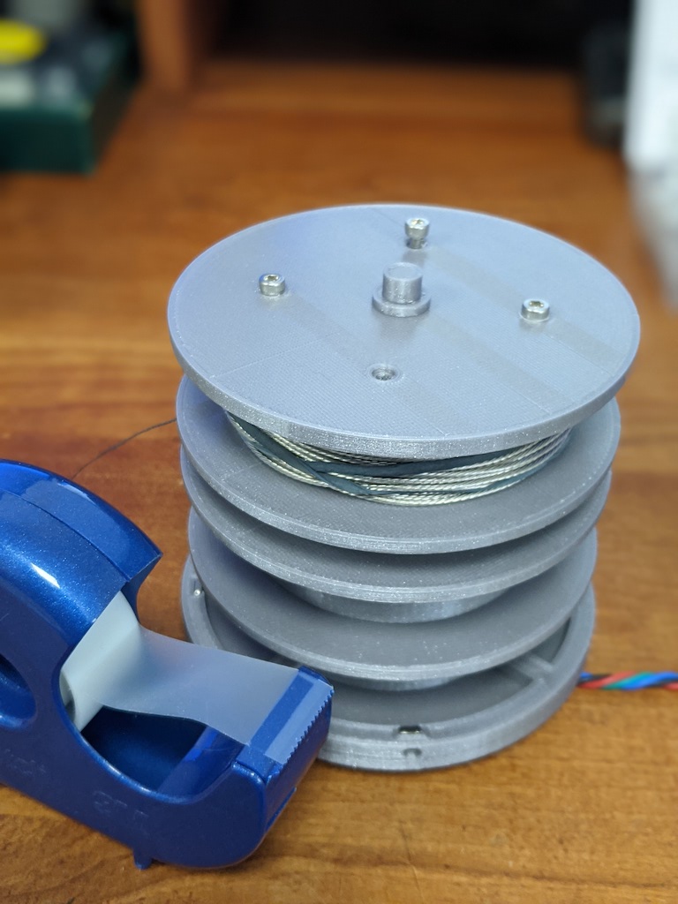
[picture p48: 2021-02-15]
Collateral/16. Assembled-Spools.jpg

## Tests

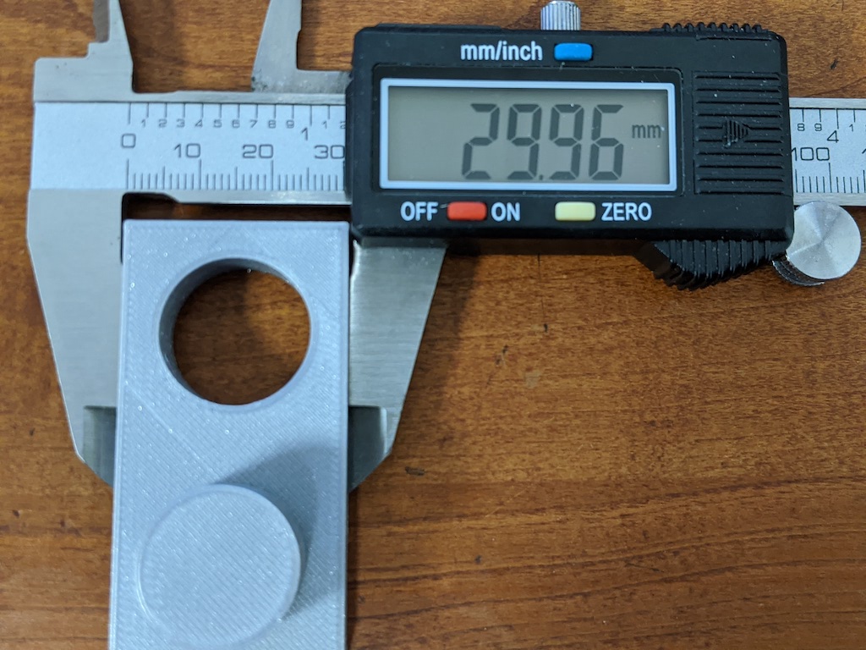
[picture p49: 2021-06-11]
Pictures/EricTest-Measured.jpg

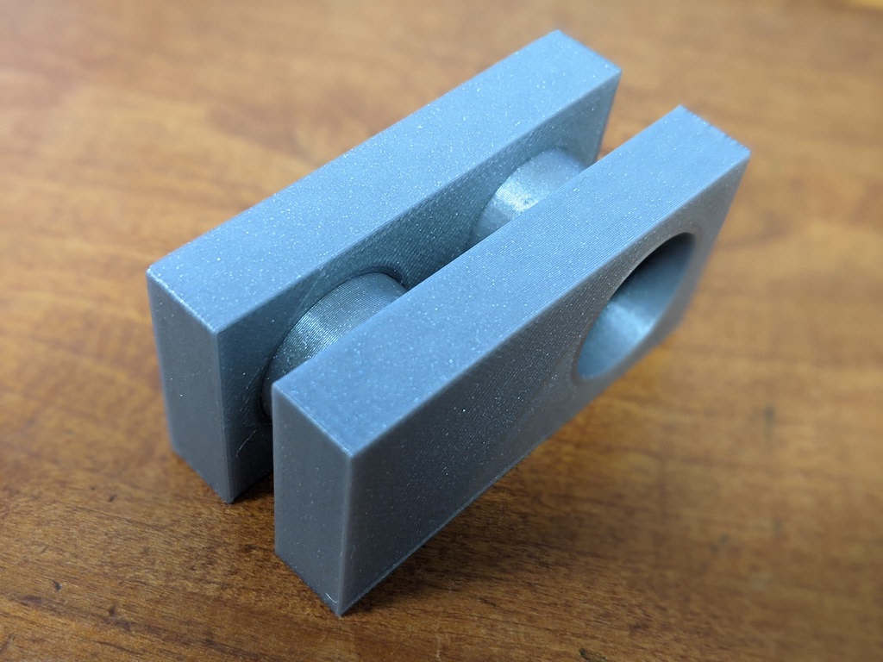
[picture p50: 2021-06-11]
Pictures/Second-Test-Adjusted-Mated.jpg

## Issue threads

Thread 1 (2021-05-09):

STL's need a bit of clearance built in

VE7OES, 2021-05-09:
I have printed all the stl's  and have found that the clearances to be extremely tight. For example the conical top needs a couple of millimetres added to the side skirts. I had to use a knife to carve out about 2mms around the circumference on the inside in order to be able to get the 3mm capacities to engage with the nuts in the inner piece. BTW those nuts definitely need more support on the back. The hole for the stepper is so tight I had difficulty getting it into the recess.
You need a BOM for the different lengths of screws, and a note that button head screws are needed in the stepper area to both mount the stepper and the stepper platform.
I'm having a bit of difficulty figuring out how to get both the wire and fishing line on the spoils without having to disassemble the unit multiple times. And then there's the matter of attaching those items to the spools.

I was able to buy the motor brushes from eBay, they can from England!

I'm stumped on how to get the json files to 'work' . Do I need to setup a mini webserver in order to 'run' them?

I think that this is a great first iteration of this, and I've shared this project with others in my area. At least one has expressed an interest in this.I

Thanks for an interesting project.

Hans/VE7OES

AD0MZ, 2021-05-10:
Dear  VE7OES - Hans:

I feel bad that your parts turned out too big.
If you wish, I could create a new STL for the cone (or any other part), using any modification you wish.

For instance, the flange at the base of the cone is  drawn to be 116 mm in diameter on the outside, and 108.2 mm diameter on the inside.
	(The case is drawn at 100 mm inside and 108 mm on the outside.  The .2 mm difference makes for a smooth but easy interference fit for me.)
The flange  is drawn at 10mm tall, but would be easy to make taller.
The screw holes are drawn with their center 4mm from the bottom of the flange.  This would be an easy change as well.

You could also sketch something you might be thinking of, and I can see what I can do.

Eric

BTW…

All the source files are in OpenSCAD format - which is plain text and full of sometimes-useful comments.
I had a lot of fun learning OpenSCAD.  You write descriptive “programs” to describe your parts rather than trying to align things with a mouse.
OpenSCAD is a little strange at first and requires a bit of trial and error, but results in very precise drawings and exports STL files natively.
(Even the animations on the Github page at done OpenSCAD using the actual parts! )

BTW.
BTW.

The WIFI stepper responder to simple HTML “get” requests…
If you don’t want to set up a Node-Red environment, you can also simply code a web page with URL’s that command the motor to go where you want.

(The WIFI Stepper has examples on its Quick Start Page - just use the default access point and open with any browser.
I can extract the formulas and the URLs (to GET) from the JSON if that would help as well.)
I’ve tested a simple page to test a standalone system and found ti to work just fine.  (I don’t know enough HTML to make a pretty app though.)
You could even use CURL from a command prompt and issues your commands via a script or two!

(I may work on a simple web page interface later this fall so that the hardware is simpler and cheaper.
Still assuming a WIFI Stepper branded controller, as it takes all the work out of moving a stepper motor.  (Acceleration and stall detection for example)
It also seems to be the cheapest way to get controller with WIFI, a web server, and a good stepper driver chipset.)

I used Node_Red because many here in the US use it and I wanted to learn it.

Sincerely:
Eric
AD0MZ

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

VE7OES, 2021-05-10:
Hi Eric!

I think I should preface this with an apology that I'd had a bad time with
a number of things including acquiring the Setter board.  Just so you're
aware, I ordered the board and at the appropriate time I got an email that
the board and stepper had shipped. So I waited and waited and waited some
more.  Within the first week UPS site started saying that it was sitting in
a secure pending customs.  And that's where it sat.  I let this drag on for
a month before my frustration overcame me and I tracked down a phone number
for UPS.  On calling them I was told that the seller had said to send it
back!  And I had not been contacted by anyone.  I attempted to contact
CrowdSupply with no luck.  I went to a local UPS store and all I got was
another phone number.  This time when I called, I got some-one that was
willing to do some digging. ChrowdSupply happened to have a link to a 3rd
Party tracking site and on using it to track the package, I was able to say
that the package was still at the facility.  I mentioned this and the gal
agreed.  So she asked some qeustions and noted to me that they had tried to
contact CrowdSupply for some information several times but got nothing.
Anyway the packaged was processed on my information, and I pad the
customs and import fees and received the package finally. Whew! What an
ordeal!

I'd spent some time trying to trim the different parts to be able to
assemble it pre receiving the motor and board, so found I had these issues
already.

Anyway, I've had some time to calm down, so sorry for going off like that.

I've decided to take the plunge and see if I can figure out both Node Red
and OpenSCad.  I think I'll see about working through a few Tutorials and
see what comes of it.  If I should happen to come up with something that
works for me, I'll definitely share it with you.

One of the things I'd like to attempt is to take what you have and add
50MHz, 2 Meters, and 70 cm.  My thoughts are that because the lengths of
wire are so short, perhaps it's possible to use a multiple of 3 times that
length for those frequencies as the wire length.  I have a friend that's
very knowledgeable in the RF side and that's what he told me the lengths
would need to be for multiple lengths at frequency.

Also noticed that the board has an ADC on it run by the ESP32 chip.  I'm
thinking that perhaps the firmware of the board could be extended to add an
SWR meter, perhaps forward and backward.  It's a long shot...  About 30
years ago I did some microprocessor programming.

Anyway the first thing I need to do is finish getting the wire and fishing
line on it and then mounting it.  My current thought is to drill some small
holes on either side of one of the long screws that go through all the
rotating parts and use that as a fastening point for these items.  It might
be worth while to look at heat set brass inserts at the top end to take
some of the strain and to handle the screwing and unscrewing ot these four
bolts that looks like is required. They make them for three mm bolts with
4.6mm OD diameter for the insert and a length of 3.0 mm or 3.6mm or 3.8 mm.
Just for fun, I may try drilling the bosses out a bit to ~4 mm and then
heat setting a few.

Thanks for your time, 73.

Hans/VE7OES

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

AD0MZ, 2021-05-11:
Dear VE7OES - Hans:

I had similar trouble with the second controller I ordered.
Website said in stock, ships next week.  Waited two months.

I noted at that time that their webpage and kickstarter sites are very stale.
While I think it’s an excellent product and the price is OK,  I’m nervous about the company.
These factors are while I plan to learn either ESP32, or some type of Opto-Serial controlled driver in the fall.

A couple of friends have asked about other band coverage.
I used a simple function to determine element length, so just adding buttons to the Node-Red Flow would simply work.
If you want to use indirect relationships for element length, a it would take a little logic - but still easy.

(I converted all the ham bands to millimeters, and then just multiplied steps times circumference at an average depth in the wire spools.
I used a spreadsheet to find a constant, that I could store in a global variable  —  and use that  in a single function that forms the URL that commands the stepper.)

BTW…  I just drilled a hole in the spool and stuck the wire or string through it - with a knot.  Printing a hole is on my improvement list.

Best wishes:
Eric.

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

VE7OES, 2021-05-23:
Hi Eric,

I haven't been able to get very far using you software. I did find the
hardcover IP address in the main file and changed to the the board default
when it's new and unconfigured, 192.168.4.1. I was able to connect to it,
and have tried a couple of times to configure it for I home network with
not luck, I'm sure it's something small I'm missing.

I loaded termux on my tablet and from there node-red. When I load
Tuner-APP.Jason I get the dev interface and can see in the one section
where the URL 's are used. I've deployed the app and brought up the ui but
when I go to run out wire to say 10m, it just moved 1 step on the motor and
stops. Switching to another band and I get the same results. I do see a
complaint in termux about "Unknown context store 'file'...."  Not sure if
the utility json app is supposed to generate that but I'm not sure what to
do with that file.

I do know the board works since when I do
~/compass $ curl -sS "
http://192.168.4.1/api/motor/run?dir=forward&stepss=100"
The stepper rotates just fine.

Hope you can shed some light on this.
I plan to spend some time going through your code to try and understand
what's going on so I can add the other band; thanks for the hints.

Once I get the stepper rotating properly, under control, I'll put some wire
on the spools and then fishing line.

I showed off what I have in a zoom meeting today and got a few more
enquiries on where to find info.

Hans
VE7OES

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

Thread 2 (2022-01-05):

Can we work to improve this?

WA1RCT, 2022-01-05:
Hi Eric,
  This looks really cool.  I was thinking of doing something like this myself, and would like to try to make a version that I could use as my primary antenna.  I think there are a number of areas that would need to be modified so that it would survive outdoors and be reliable.  I'd like to work on that.  I'm a electrical/software engineer by profession, but do not have training in mechanical design.  Could you reply with your email address, and I can reach out to you, and see if there are things I could work on.

Thanks,
Dave Hempstead
WA1RCT

AD0MZ, 2022-01-06:
Dear Dave:

Thanks for the note!

I would be happy to help in any way I can to improve the antenna system.  I enjoy the engineering stuff a lot!

I have been interested in antenna physics since high school.
Having been trained as a broadcast engineer, I was always somewhat surprised by the ”If your tuner can fix the SWR - it’s good enough” attitude that a lot of HAM’s seem to operate with.
(In AM radio, we designed the antenna to be near-perfect, and then designed everything else for the best efficiency.)

The project on GitHUB was at first a platform to experiment with the physics, and mutated into a useful antenna for a friend.

I have found the prototype durable enough for temporary use like field days and similar operation.  (3 guyed 41 foot poles)
The housing is PETG rather than PLA, I had intended to paint it if needed.

 The small size is a compromise.  If I were to build another for long term use on a good tower, I’d switch to a better (bigger?) motor.
	1.	Larger diameter spools would hold thicker wire, but would require more torque than NEMA 17 (which I already had) would provide.
	2.	Wide spools would hold thicker wire, but would “wind” inconsistently resulting in tangles.

I tried a lot of iterations of various parts, and came up with the compromise that works well in my environment.

	I considered using outdoor rated PVC pipe or similar for the housing with add-on external brush-holder thingies instead of printing the whole thing.
	I tried copper alloy “brushes” with good success (Copying SteppIR), but found the replaceable carbon brushes to last well.
	From an electrical engineering point of view,  the important part is to have non-conducting spools - I don’t think a metal case would be out fo the question.
	Also tried belt drive reduction for more torque, but found it too complicated and hard to keep adjusted (Belts were hard to find the right size).
	I considered an ESP32 based system, as well as ditching the WIFI altogether and just making a USB connected controller -
		The WIFI Stepper product just made “the first try” easier since I had no experience with stepper motors.

	I am currently working on building a static web page with a tiny bit of Javascript in place of NODE-RED and the required server.
	(If you stick with the WIFI stepper product, an HTTP “get” statement is all that you need to send in order to send commands.)

I’d be interested in what you think.

Eric.

AD0MZ

***@***.***

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

WA1RCT, 2022-01-06:
HI Eric,
   Thank you so much for the quick reply.  Here are my thoughts.
   I currently have a folded dipole which works 'ok' from 160M to 10M.
I've been playing with auto tuners (built up a ATU-100 model recently), but
I agree with you that having a resonant antenna is the best starting
point.
   My personal goal would be to try to develop an antenna for my setup that
will work well across that entire range.  I have an IC-7300 rig, and run
digital often, so I would want the antenna to handle 100w-200w without any
issues.  I have fellow hams who might be interested, and they run 1kw+.
   My current dipole is 140 feet, suspended from trees, with an additional
support rope at the center point (all support ropes are on pulleys for easy
raising and lowering).  So I believe I could put some weight at the center
(even without a tower).
   I was thinking of a setup similar to your prototype, and then googled it
and found you.
   I've reached out to a friend that I previously worked with.  He is a
highly skilled mechanical engineer who has spent his career designing the
mechanical parts of medical products, including some that used small
precision motors and cables.  If he would be willing to provide any
component selection advice or provide any guidance, I think this would help
me alot.
  For me the mechanical aspects would be the biggest challenge.  For the
electrical and software, I have tons of ideas for automating the system.
I'm thinking of getting a raspberry pi to run it (and I think it can also
run your software).  I am confident I could automate this to work any way
I'd like.(I prefer fully automatic systems, and usually the best solution
is closed loop)

   From what I've seen on your website, here are my thoughts:
1) the cable/wire will need to be enclosed to work in New England (ice and
snow).  My thought is to have a rope running the entire length of the
antenna, and hanging a flexible tube under it, and the wire+rope/cable will
run completely inside the tube.  At each end there would be a pulley on a
spring (inside the tube, I've found some very small pulleys, check out
Harken) and the far ends of the tube would be sealed.   THen where it meets
the center unit, the tubes would have to be attached weathertight to the
unit.
2) I think you bring up very good points about the motor and the spools.  I
don't know the best radius to consider, but I'd have to worry about life of
the wire and the rope/cable bending so often.  Have you looked into that?
Also have you looked into corrosion on the cable, or just having the copper
build up surface resistance as it weathers?  This would create resistance
and then when coiled it wouldn't have the low resistance we need.  Have you
considered tinned wire?  Does that change the flexibility of the cable?
3) I was thinking of using small diameter dacron or dyneema rope, and then
I found some flexible wire (almost like grounding braid).  For high power,
we would need to consider heavier gauge, maybe even 12 gauge.  That will
get heavy, and be much tougher to run on the spool.
4) I like your spools.  I was thinking of using a bolt at the center as the
axle, and attaching the wire to the bolt (I had assumed 2 separate wheels,
each on a separate axle), and then the brush simply touches a bolt head
that rotates, rather than touches a moving wire.  But this would require 2
separate axles (or at least an insulator between the spool axle.
5) I don't know much about the strength of stepper motors, or how much
force you need to turn the spools.
6) I do have another friend who has a 3D printer, so I could ask him to
print up some parts for me.

Your thoughts?
Dave
WA1RCT

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

AD0MZ, 2022-01-06:
Dear Dave:

Thanks for the note.

Like you, here in Minnesota - I worried about ice a bit.
I found that if I retracted all of the wire after use,  the “rope” (60LB braided fishing line) only iced up once.
(Also limited corrosion)  (I though of putting an “Ice/water Stripper Cartridge” in the vacant pockets where the roper enters.  No testing though.
I think that weather is the main reason someone else (SteppIR?) has not ever sold such an antenna.

I would love to implement closed loop operation.  After running my 3d printer for 20 hour print jobs without issues,
I decided that as long as the stepper was powerful enough to never skip, there was not problem with home position being lost.
	(I tried a “homing routine” that would pull the wire in at reduced power, and sense the stall.
 	My 3D printer bumps the frame to find out where it is before it starts. )

More comments buried in  your text….

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

Node-Red made the software development quick and easy, but is a really FAT solution to a simple problem.
(I run the Node-Red server on a pi that serves up the webpage.  The pi does all the work.)
(Depending on the motor controller,  this could all be eliminated.)

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
going around the corner”  I ended up with 2 inch pulleys to get things the “glide”.
(Even though I have been a sailor, I never thought of Harken for supplies, a good idea!)
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
Yes,  3 inches was small enough for the motor to turn, and the small size made the entire package a LOT smaller (see pictures of my wood prototype with 6 inch spools)
After LOTS of cycles, the wire seemed OK with anything over 1.5 inches.

> Also have you looked into corrosion on the cable, or just having the copper

> build up surface resistance as it weathers?

> I do use “tinned” cable and retract after use.  Had no real corrosion after a summer outside.

>   This would create resistance
> and then when coiled it wouldn't have the low resistance we need. Have you
> considered tinned wire? Does that change the flexibility of the cable? Not much!

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
That would work!  As long as you “wind in” as much as you “wind out” - hence the couple spools.
SteppIR uses two spools, but still “rubs” a brush on the wire itself.

Mr friend suggested using insulated wire and a central brush, but I explained that the resulting coil would be really bad.  See GitHUB illustration.

Another option that would help with weather is to modify the RTV80 by W4QJP so that the wire is out all the time, and the ropes just move the “fold point” back and forth!
(No brushes!, except for the moving shorting contract at the moving ends.  maybe less critical?)

> 5) I don't know much about the strength of stepper motors, or how much
> force you need to turn the spools.

The NEMA 17 (when driven in micro step mode) had more than enough power for a 3 inch spools and system friction.
It was barely adequate with 6 inch spools, but a reduction drive or bigger motor would fix this.
SteppIR uses a pretty big motor for its “tapes”.

You can buy some pretty big stepper motors for less than $100.  You can also buy some closed loop motors for $350.  (yikes)
Maybe a DC motor with a position encoder could move anything...

> 6) I do have another friend who has a 3D printer, so I could ask him to
> print up some parts for me.

The whole thing could be made with hardware store parts (Pipe, external fittings, etc.)
More ugly but probably more robust for a tower installation.

Maybe a cross between my plastic parts and the Collins hand-powered winch.
https://www.ebay.com/itm/184927161352?hash=item2b0e848c08:g:AzkAAOSwc~Nfqxbt <https://www.ebay.com/itm/184927161352?hash=item2b0e848c08:g:AzkAAOSwc~Nfqxbt>

Good luck.
I’d love to see such an antenna really high up!  Too bad a big high dipole (Even fixed) is a lot of trouble.
If I were still on the farm with my 10 acre farmstead, I would take what I’ve learned and put an 8 inch across, 18 inch high plastic Nema box upstairs,
and just print a few internal parts for spools and brushes.)  I think that using a 200lb test monofilament might not have much ice sticking to it?

Of course a perfectly resonant dipole is 70 ohms, so perfection is still ways off :-)

In AM radio, we used a “matching network” (NOT a TUNER according to the chief engineer)
to get from the antenna’s impedance to something around 600 ohms (if I remember from the 70’s)

Eric.

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

WA1RCT, 2022-01-06:
Thanks Eric,  Could you send me your email address, and we can continue
this separately?
Dave

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
